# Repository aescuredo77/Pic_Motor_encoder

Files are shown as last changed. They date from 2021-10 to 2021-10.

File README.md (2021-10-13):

# Pic_Motor_encoder
The  I2C ServoMotor can serve different purposes, for example, like servo that we need positioning and hold, while the diffrobot we are interested in speed. 

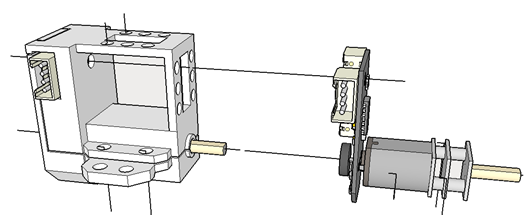
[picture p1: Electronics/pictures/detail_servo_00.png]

 
 **ServoMotor detail of the interior circuit** 

## Description ##
The servomotor consists of a controller board with a PIC16f1503 and a LB1938FA driver, which drive a Pololu &quot;Micro-metal-gearmotors&quot; type reduction motor. The reduction of the motors is based on the need for example:

- 100: 1, 130 rpm
- 298:1, 45 rpm

The microcontroller communicates through I2C, which allows us to connect 127 nodes in series. There will not be so many in our applications, we have asked for LP motors, Low power because they have a low consumption that allows us to connect them in series.

The I2c address will depend on the application that we are going to make, it should not be a problem to change it depending on the needs, but we are going to give a few premises. The I2C addresses are defined by 7 bits, the least significant bit tells us if it is writing or reading, so we will give a couple of addresses, the first is the one recorded in the pic, and the other is the one we will use in the Arduino / teensy to communicate. Always in Hexadecinal.

| Name | Mode | address | address Arduino |
| --- | --- | ---| ---|
|Servo_Motor_Left | speed  | 0x22  | 0x11 |
|Servo_Motor_Rigt | speed  | 0x20  | 0x10 |
|Gripper | position | 0x10  | 0x08 |
|Servo_base | position | 0x30  | 0x18 |
|Servo_left | position | 0x32  | 0x19 |
|Servo_right | position | 0x34  | 0x1A |

The 12 pulses per turn encoder must be multiplied by the reduction of the motor to obtain the pulses per turn that the motor will give.For example in the case of reduction 100:1 the servoMotor needs 1200 pulses to complete a lap.

## Boards and Schematics ##

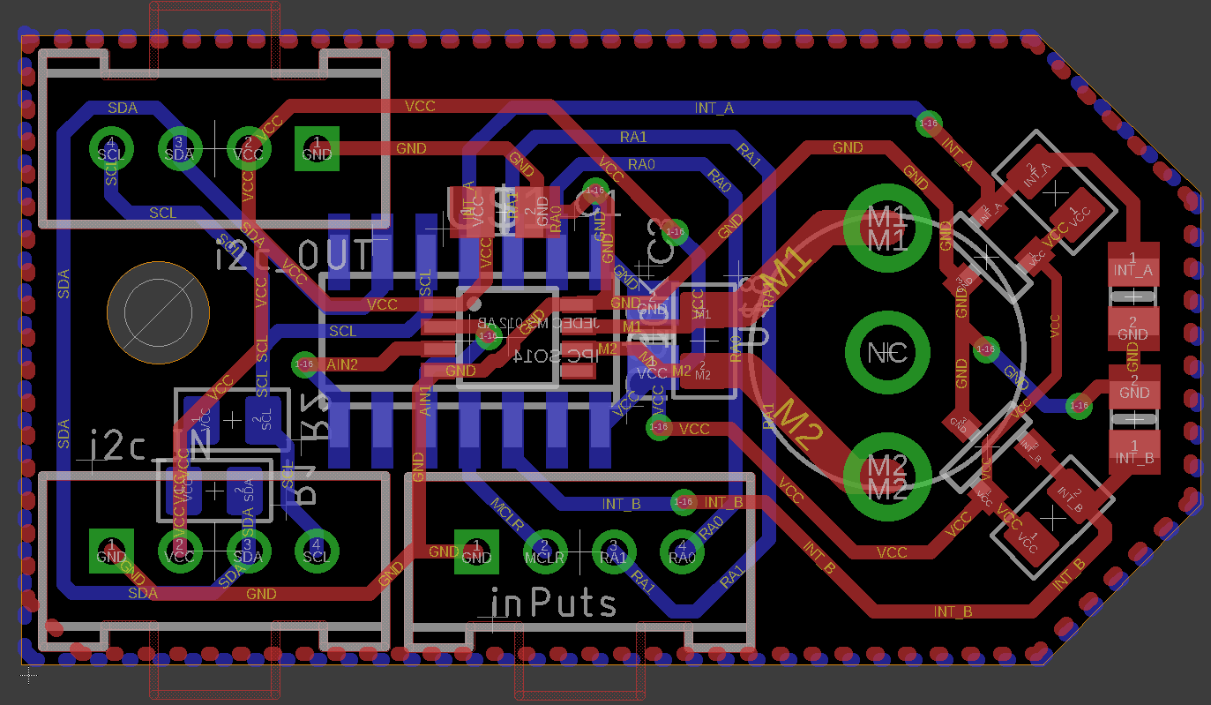
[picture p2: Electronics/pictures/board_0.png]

**ServoMotor board in Eagle**

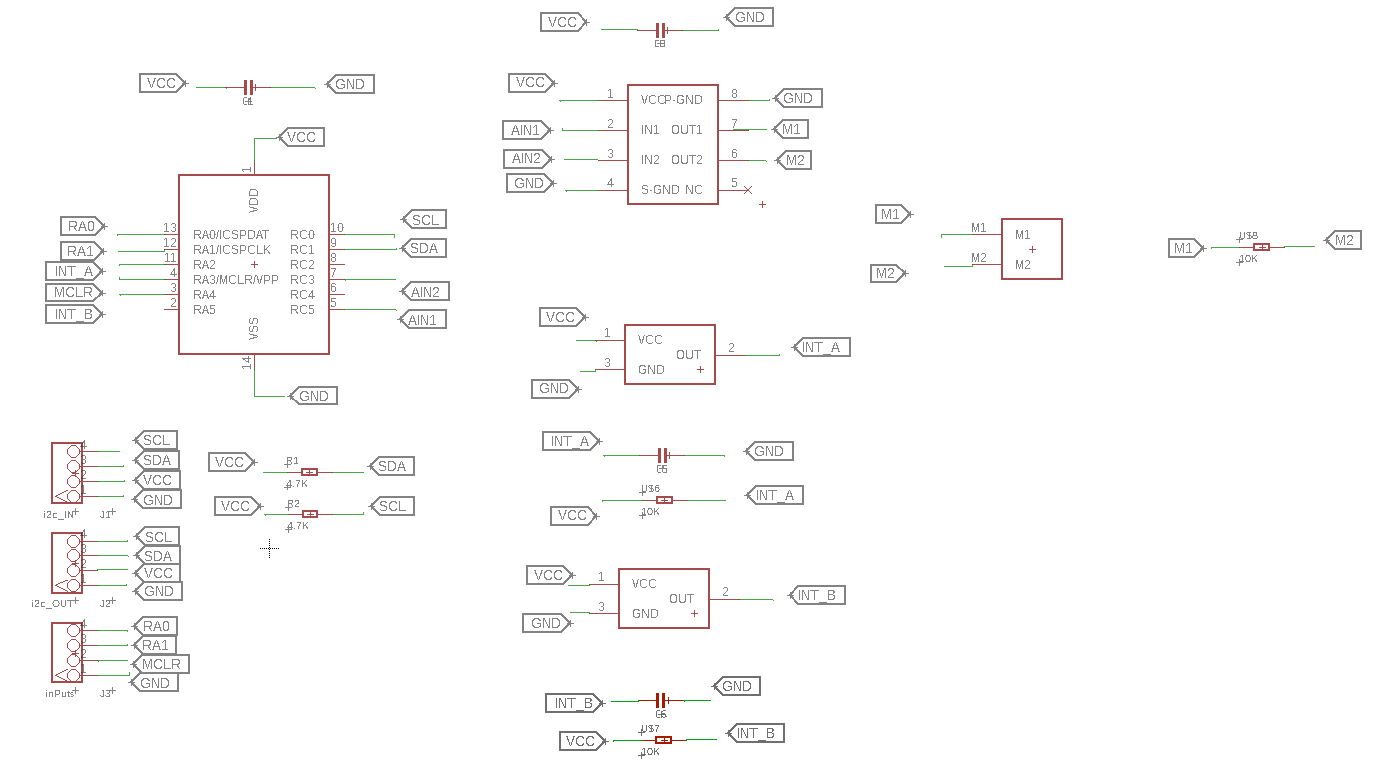
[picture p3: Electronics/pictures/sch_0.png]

**ServoMotor schematic in Eagle** 

## Electronics  

[PIC16F1503](http://ww1.microchip.com/downloads/en/DeviceDoc/40001607D.pdf) 14 pin Flash, 8 bit microcontroller, 16Mhz internal Oscillator, 2Kwords linear program, 128 data SDRAM, 8 Analog to Digital converter at 10 bit resolution, 4 PWM, 3 Timers, I2C/SPI.

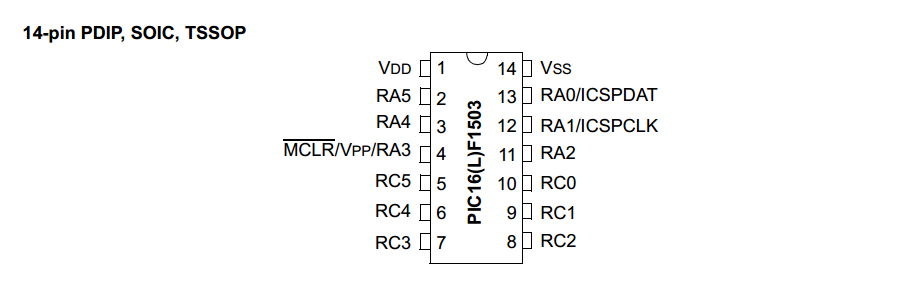
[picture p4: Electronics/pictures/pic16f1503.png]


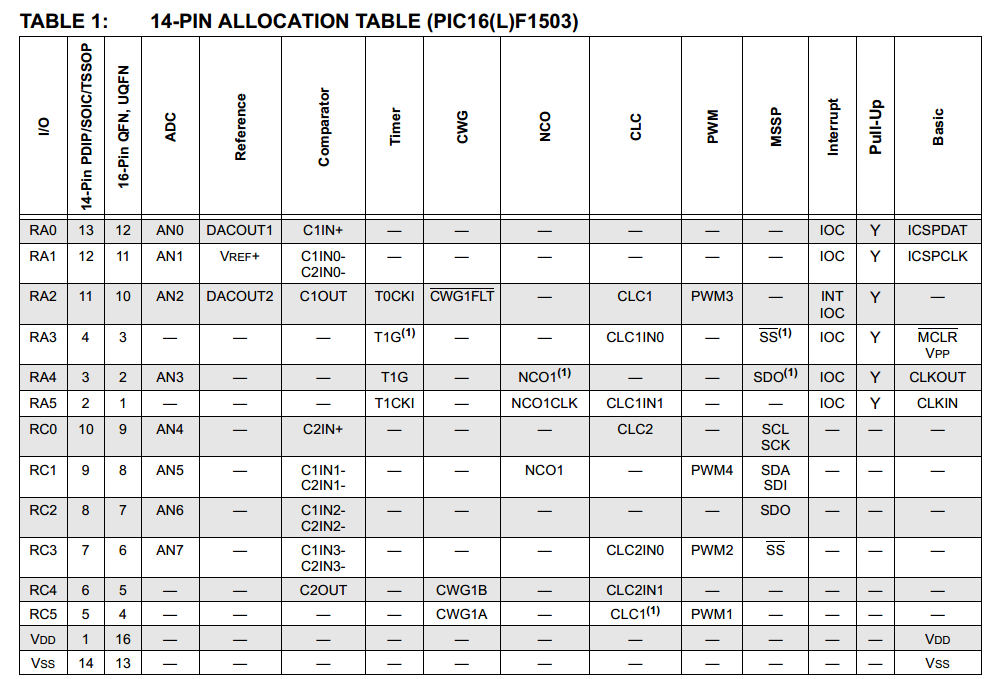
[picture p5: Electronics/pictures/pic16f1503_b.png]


The driver is [LB1938FA](https://www.dropbox.com/s/l5har1ai8nknbxs/LB1938FA.pdf?dl=0), It is a driver configured in H-bridge that allows us to control the motor in speed and direction with only two inputs. Analyzing the driver that the DFRobot servomotors carry, the L9110S looks for alternatives because the aforementioned driver is a little out of print or is only sold on pages of doubtful reliability.

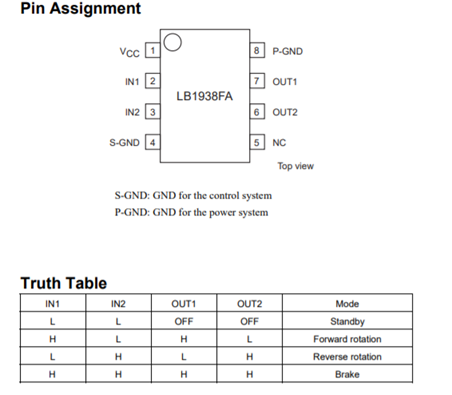
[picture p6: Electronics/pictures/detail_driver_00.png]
 

 **LB1938FA is the cousin of the L9110S carried by Dfrobotics servos.** 

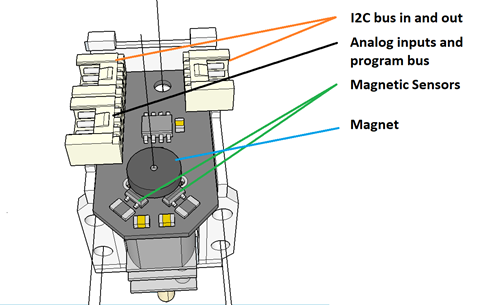
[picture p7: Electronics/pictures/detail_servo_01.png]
 
 
 **Detail of the motor control board** 

#### Note: For a Diffrobot model the motor on the right is mounted in the opposite direction from that on the left. The micrometal motor gearboxes are not symmetrical. In this way we equalize the mechanical behavior. #### 

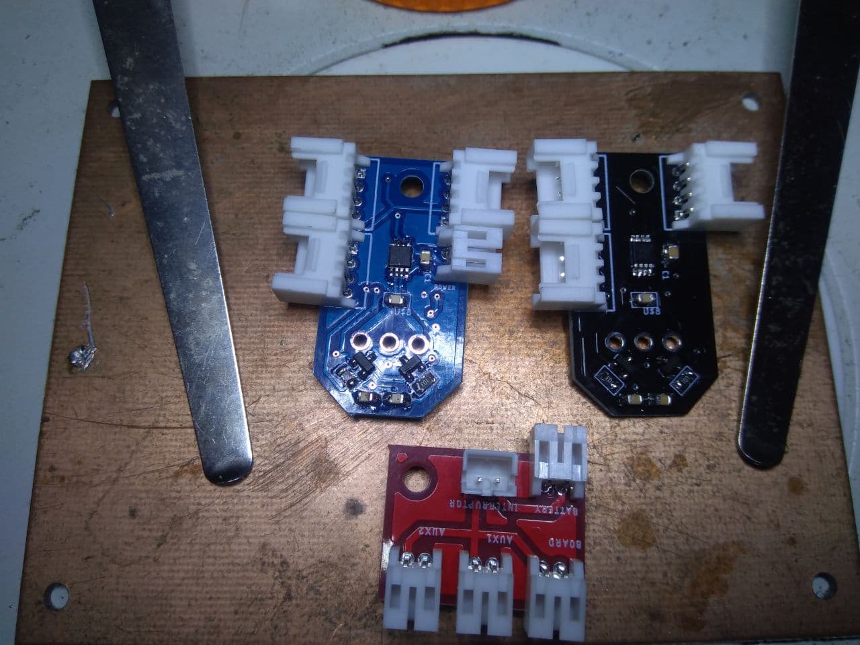
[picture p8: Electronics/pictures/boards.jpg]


If you need more powerful motors or those that require a greater workload, there is a version of these servos with an independent power supply from the motors.

## Sottware ##

The "/Electronics/src/" folder contains the versions of the PIC program for operating the  left/right servoMotor. Different programs are needed because the motors are reversed. We can use this program for any application, gripper or servoPosition or continuous servo. 

To use it in both arduino and teensy or similar, a library has been made in c++ that is in the arduino folder.

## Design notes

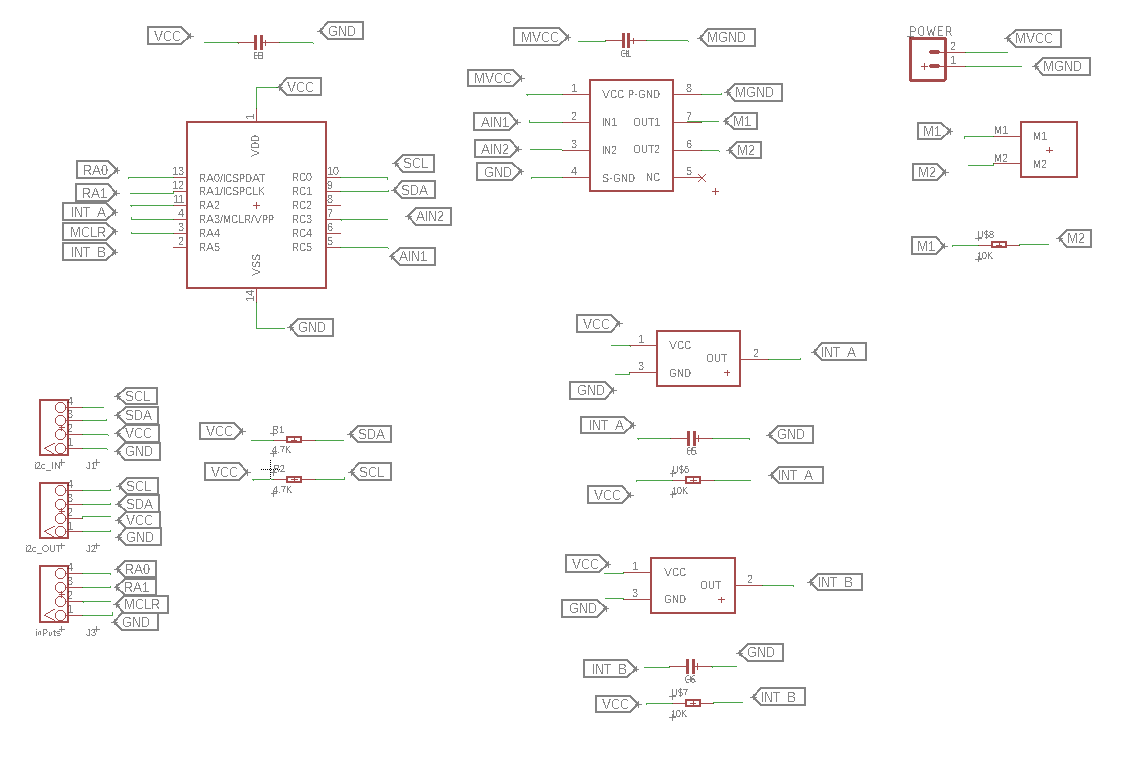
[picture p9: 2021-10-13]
Electronics/pictures/sch_1.png

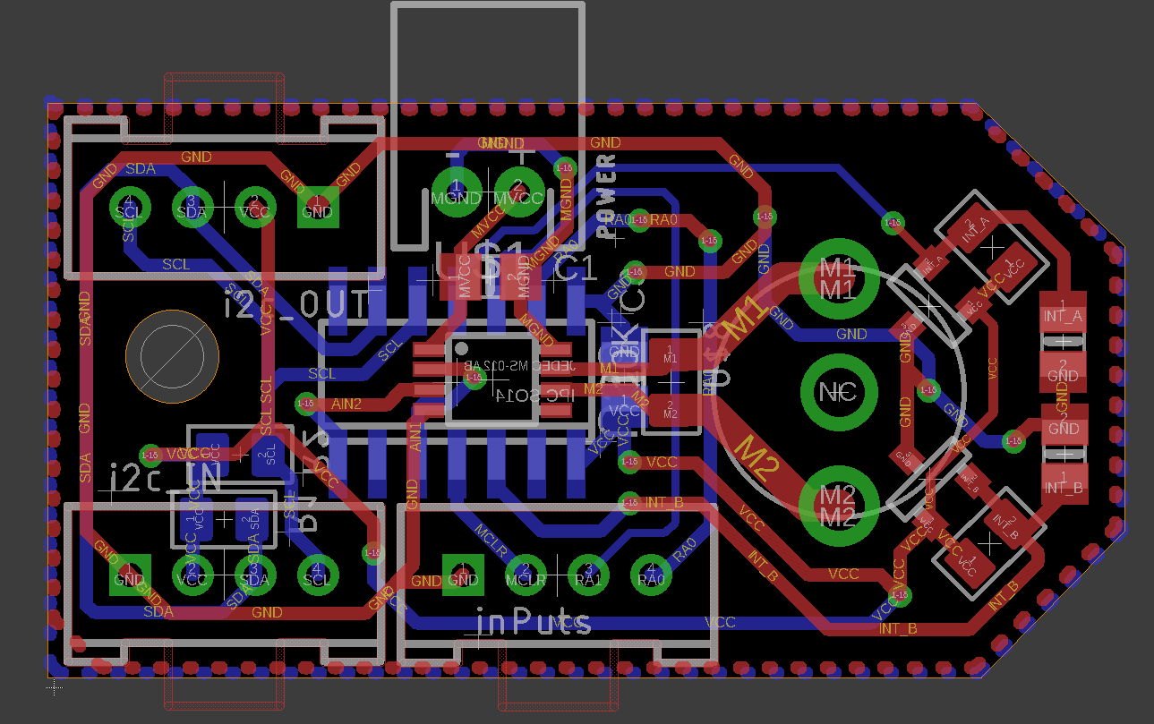
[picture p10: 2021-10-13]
Electronics/pictures/board_1.png

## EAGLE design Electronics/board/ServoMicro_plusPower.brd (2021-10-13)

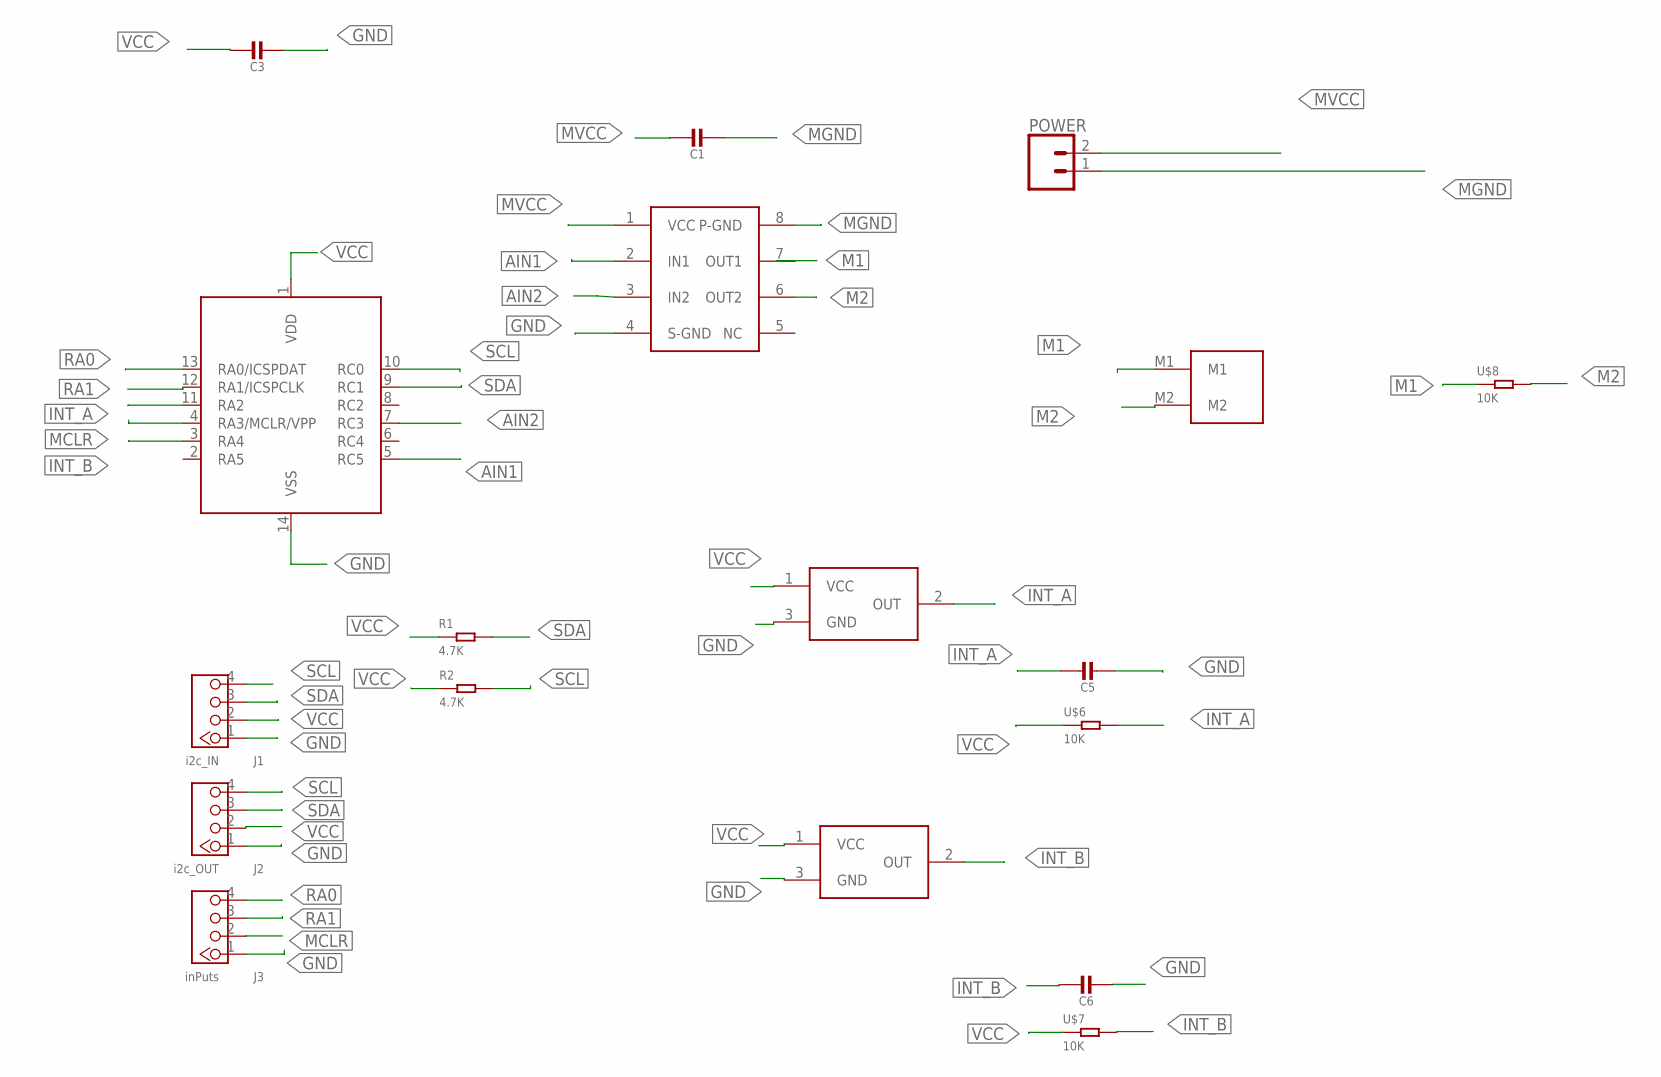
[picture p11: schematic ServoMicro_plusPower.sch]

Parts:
C1, C3, C5, C6: CAP_CERAMIC0805-NOOUTLINE; 0805-NO
J1: i2c_IN; HW4-2.0
J2: i2c_OUT; HW4-2.0
J3: inPuts; HW4-2.0
POWER: CONN_02-JST-2-PTH-NO_SILK; JST-2-PTH-NS
R1, R2: 4.7K; R0805
U$1: LB1938DFA_A; MSOP8
U$2, U$3: DRV5021-Q1; SOT-23
U$4: MICRO_MOTOR
U$5: PIC16F1503SOIC; SO-14
U$6, U$7, U$8: 10K; R0805

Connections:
AIN1: U$1.2 (IN1), U$5.5 (RC5)
AIN2: U$1.3 (IN2), U$5.7 (RC3)
GND: C3.2, C5.2, C6.2, J1.1, J2.1, J3.1, U$1.4 (S-GND), U$2.3 (GND), U$3.3 (GND), U$5.14 (VSS)
INT_A: C5.1, U$2.2 (OUT), U$5.11 (RA2), U$6.2
INT_B: C6.1, U$3.2 (OUT), U$5.3 (RA4), U$7.2
M1: U$1.7 (OUT1), U$4.M1, U$8.1
M2: U$1.6 (OUT2), U$4.M2, U$8.2
MCLR: J3.2, U$5.4 (RA3/MCLR/VPP)
MGND: C1.2, POWER.1, U$1.8 (P-GND)
MVCC: C1.1, POWER.2, U$1.1 (VCC)
RA0: J3.4, U$5.13 (RA0/ICSPDAT)
RA1: J3.3, U$5.12 (RA1/ICSPCLK)
SCL: J1.4, J2.4, R2.2, U$5.10 (RC0)
SDA: J1.3, J2.3, R1.2, U$5.9 (RC1)
VCC: C3.1, J1.2, J2.2, R1.1, R2.1, U$2.1 (VCC), U$3.1 (VCC), U$5.1 (VDD), U$6.1, U$7.1

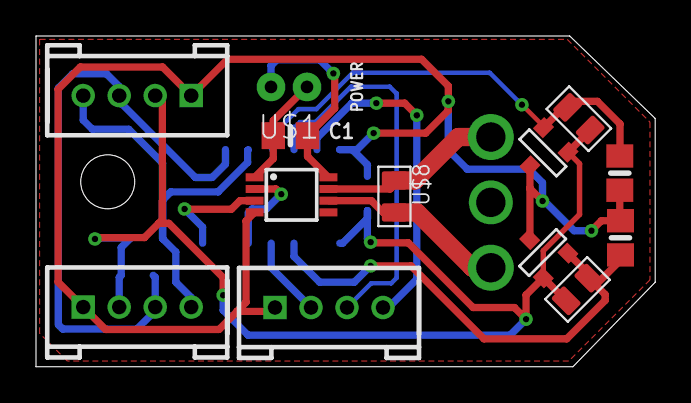
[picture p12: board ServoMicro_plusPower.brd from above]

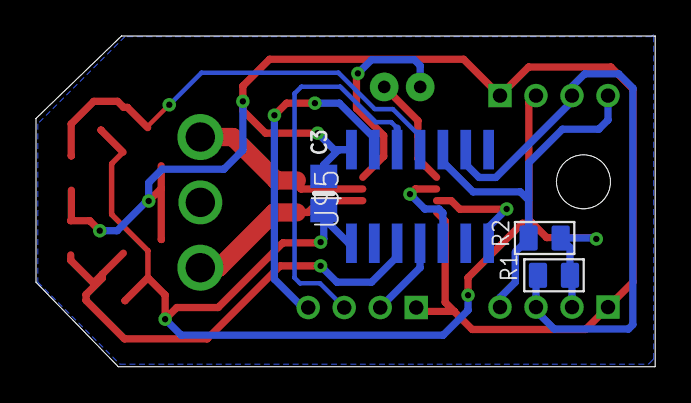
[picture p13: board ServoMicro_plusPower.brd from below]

Board: 2 copper layers, 34.4 x 18.4 mm, 18 parts (4 on the bottom side), 15 nets.

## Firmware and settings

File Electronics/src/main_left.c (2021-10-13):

#include <main.h>
#include <stdlib.h>

#INT_RA
void  RA_isr(void) 
{
   int8 value;
   int8 new=input_a()&0x14; //Masks A2 & A4
   value=new^old;
   if(value!=0){
      if (interrupt_active (INT_IOC_A2)){
      clear_interrupt(INT_IOC_A2);
            if (input(PIN_A2))
             {  
               //ext_int_edge(H_TO_L);
               if (input(PIN_A4))contador++;   // if -- right  ++ left
               else contador --;
      
            }
            else                        
            {  
               //ext_int_edge(L_TO_H);
               if (input(PIN_A4)) contador--;
               else contador ++;
            }
      }
      else if(interrupt_active (INT_IOC_A4))
      {
      clear_interrupt(INT_IOC_A4);
         if (input(PIN_A4))
             {  
               //ext_int_edge(H_TO_L);
               if (input(PIN_A2))contador--;
               else contador ++;
      
            }
            else                        
            {  
               //ext_int_edge(L_TO_H);
               if (input(PIN_A2)) contador++;
               else contador --;
            }
  
      }
   }
 old=new;     
}

#INT_TIMER2
void  TIMER2_isr(void) 
{
    if(check==0){ // modo velocidad
      if(dir==1) { //CW
          set_pwm1_duty(pwm);
          set_pwm2_duty(min);
      }else if (dir==2){ //CCW
         set_pwm1_duty(min);
         set_pwm2_duty(pwm);
      }
      else{//stop
         set_pwm1_duty(min);
         set_pwm2_duty(min);
      }
   }
   else if (check==1){ // modo posicion 
   
      test=pulsos-contador;
      if(abs(test)>10){
      //if(pulsos!=contador) {
      
         if (pulsos>contador) {
            set_pwm1_duty(min);
            set_pwm2_duty(pwm);
         } else if (pulsos<contador) {
            set_pwm1_duty(pwm);
            set_pwm2_duty(min);
         }
      } else {
        contador=pulsos;
        set_pwm1_duty(min);
        set_pwm2_duty(min);
      }
   }

}

#INT_SSP
void  SSP_isr(void) 
{
   
   int state, incoming;
   state = i2c_isr_state(I2CS); 
   if(state < 0x80) //master sending Data <128
    { 
        incoming = i2c_read(I2CS); 
        if (state == 1) 
        { 
            cmd = incoming; 
        } 
        
        else if (state > 1) 
        { 
            rcv_buf[state-2]=incoming; 
        } 
    } 
        
    else if (state==0x80)
    { //disable_interrupts(INT_EXT);
      dato[0]=make8( contador,0);
      dato[1]=make8( contador,1);
      i2c_write(I2CS,dato[aux]);
      aux++;
      if(aux>1) aux=0;
      //enable_interrupts(INT_EXT);
	  restart_wdt();
    }
}



int16 convert(int pwm)
{
   int16 bux=0;
   float coe=(max-min)/255;
   float aux=pwm*coe+min;
   bux=aux;
   return bux;
}

void main()
{
  setup_timer_2(T2_DIV_BY_16,156,16);      //628 us overflow, 10,0 ms interrupt
   //enable_interrupts(INT_EXT);
   setup_wdt(WDT_128MS);
   enable_interrupts(INT_RA);
   enable_interrupts(INT_IOC_A2);
   enable_interrupts(INT_IOC_A4);
   enable_interrupts(INT_TIMER2);
   enable_interrupts(INT_SSP);
   
   enable_interrupts(GLOBAL);
   
   setup_pwm1(PWM_ENABLED|PWM_OUTPUT); 
   setup_pwm2(PWM_ENABLED|PWM_OUTPUT); 
   set_pwm1_duty(min);
   set_pwm2_duty(min);

   while(TRUE)
   {

      
     switch(cmd)
     {
       
       case 0x10://Direction motor control 
         check=0;
         dir=rcv_buf[0];
         pwm=max;
         break;
       case 0x11://Direction and speed motor control
         check=0;
         dir=rcv_buf[0];
         pwm=convert(rcv_buf[1]);
         break;
       case 0x20://Position motor control
         check=1;
         pulsos=rcv_buf[0];
         pulsos=pulsos<<8;
         pulsos|=rcv_buf[1];
         pwm=max;
         cmd=0;
         break; 
       case 0x21://Position and speed motor control
         check=1;
         pulsos=rcv_buf[0];
         pulsos=pulsos<<8;
         pulsos|=rcv_buf[1];
         pwm=convert(rcv_buf[2]);
         cmd=0;
         break;   
       case 0x30:// Read contador variable
         dato[0]=make8( contador,0);
         dato[1]=make8( contador,1);
         cmd=0;
         break;
       case 0x40://
         contador=0;
         pulsos=0;
         cmd=0;
         break;   
       } 
   
   }
      
  

}
